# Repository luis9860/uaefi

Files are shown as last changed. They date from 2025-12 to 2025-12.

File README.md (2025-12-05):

# Ultra Affordable EFIi

🟢[$175 base model rusEFI store](https://www.shop.rusefi.com/shop/p/uaefi-ultra-affordable-efi)🟢

## Community Support

🔴Community support ONLY 🔴 https://www.facebook.com/groups/rusEfi 🔴 [Discord](https://github.com/rusefi/rusefi/wiki/Discord)🔴 [Commercial Support](https://www.shop.rusefi.com/shop/p/details-about-rusefi-ecu-technical-support) 🔴

## Technical Details

Open Source KiCAD hardware powered by [Hellen-One](https://github.com/andreika-git/hellen-one)

Powered by [rusEFI firmware](https://github.com/rusefi/rusefi)

[User Documentation](https://github.com/rusefi/rusefi/wiki/uaEFI)

x

x

## MCU options

1mb of flash is _required_.

One day we shall try https://jlcpcb.com/partdetail/Stmicroelectronics-STM32F427VIT6%2FC57097#EC or https://jlcpcb.com/partdetail/Stmicroelectronics-STM32F437VIT7%2FC1338578#EC

## rusEFI Store

https://www.shop.rusefi.com/shop/p/uaefi-ultra-affordable-efi

## HOWTO JLCPCB

You would need three files from ``boards/uaefi-a/board`` folder to place your JLCPB Assembly order: gerber.zip BOM-JLC.csv and CPL.csv

### Q: having trouble with opening uaefi board project. library path seems ok, i do not know how to solve missing modules issue

A: missing modules are closed source. they are filled in by github magic
github magic combines gerbers and spits out a complete bom/pcl/new gerbers to upload to jlc/friends. See https://github.com/rusefi/hellen-one/tree/master?tab=readme-ov-file#tldr for more info

### Q: Magic modules? How do I see schematics of those?

A: https://github.com/rusefi/hellen-one has full documentation for each module

### Q: Something wrong with BOM?

A: Nope, that's normal nothing to worry about click 'Continue'.



### Q: how do I get more RAM for Lua?

A: fabricate with STM32F42xVI firmware would defect extra RAM and give you extra Lua. Once your script does not fit into STM32F42xVI it's F7 time or help us leverage F413.

### Q: I've place an order with JLCPCB and I see scary looking wrong orientation?

A: that's expected. See [boards/uaefi-c/board](boards/uaefi-c/board) ``Original*.png`` files and ``Produce*.png`` after JLCPCB manual review process.

## Bluetooth power issue fix

It was found that board with installed BT module may be affected by power issue.

During power on BT module consume too much inrush current on 3.3V line causing 3.3V drop below MCU reset hreshold. This may lead to unstable start or infinity reset loop.

To fix this please install additional capacitors to 5V and 3.3V powerlines.

Polarized electrolytic capacitors with at least 10V rating and extended temperature range are recommended. Tantalum and solid electrolytic capacitors are also suitable.

**Please carefully follow illustrated polarity.**

33..47uF should be added to 5V powerrail. [This](https://www.digikey.com/en/products/detail/w%C3%BCrth-elektronik/860020372004/5727028) or [this](https://www.digikey.com/en/products/detail/w%C3%BCrth-elektronik/860080372001/5727224) or [any of these](https://www.digikey.com/en/products/filter/aluminum-electrolytic-capacitors/58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).



And 220..470uF should be added to 3.3V powerrail. [This](https://www.digikey.com/en/products/detail/w%C3%BCrth-elektronik/860010273011/5726952) or [this](https://www.digikey.com/en/products/detail/w%C3%BCrth-elektronik/860020273011/5727148) or [any of these](https://www.digikey.com/en/products/filter/aluminum-electrolytic-capacitors/58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).



## HOWTO EGT chip

This board has a placeholder for MAX31855 (or MAX6675) termocouple-to-digital chip. **This chip is not populated by default!**

Screenshot from 2025-09-26 11-15-15

D8 is **optional** ESD protection and also is not populated by default. You need to solder U4 only, D8 is optional. All passive components are already populated.

**MAX31855** works without addtional modification.

For **MAX6675** connect EGT- to GNDA either on J2 "C" connector or just short C28 (replace with 0R).

Screenshot from 2025-09-26 11-19-41

## [EXPERIMENTAL] How to make MAX9924 work with low tooth count trigger wheel

In some cases user may need two VR inputs on UAEFI and both trigger wheels are low-tooth count.

In default configuration MAX9924 does not work with low count trigger wheels because of its "adaptive peak threshold" and its watchdog.

Screenshot from 2025-10-12 16-58-30

On UAEFI MAX9924 is configured in **A2 mode**.

Screenshot from 2025-10-12 16-59-49

**B mode** allow use of MAX9924 with low count trigger wheels. But external Bias and Thresholt voltages should be allpied. Both can be sources from UAEFI Discrete VR module.

List of modifications:
1. pin 6: ZERO_EN connect to VCC instead of GND.
2. pin 4: supply 2.5 V instead of GND
3. pin 8: EXT, supply external threshold voltage

Pins 4 and 6 needs to be lifted from PCB to be disconnected from GND. Pin 8 initially is not connected to any circuit.

Use hot air gun to de-solder whole chip. Then twist pins 4 and 6 up so both do not touch PCB. Then solder chip back to PCB

Now use thin wire to connect:
1. pin 6 to pin 10 of the same chip.
2. pin 4 to **Vref** at R769 + C754. See file:///home/work/rusefi/docs/uaefi-d-ibom.html for its locations
3. pin 8 to **thresh_high** at U756 pin 1. See file:///home/work/rusefi/docs/uaefi-d-ibom.html for its locations



Now MAX9924 VR input uses same threshold vs RPM settings that is set for Descrete VR input. And it is cabable to work with low tooth count trigger wheels without noise issues.

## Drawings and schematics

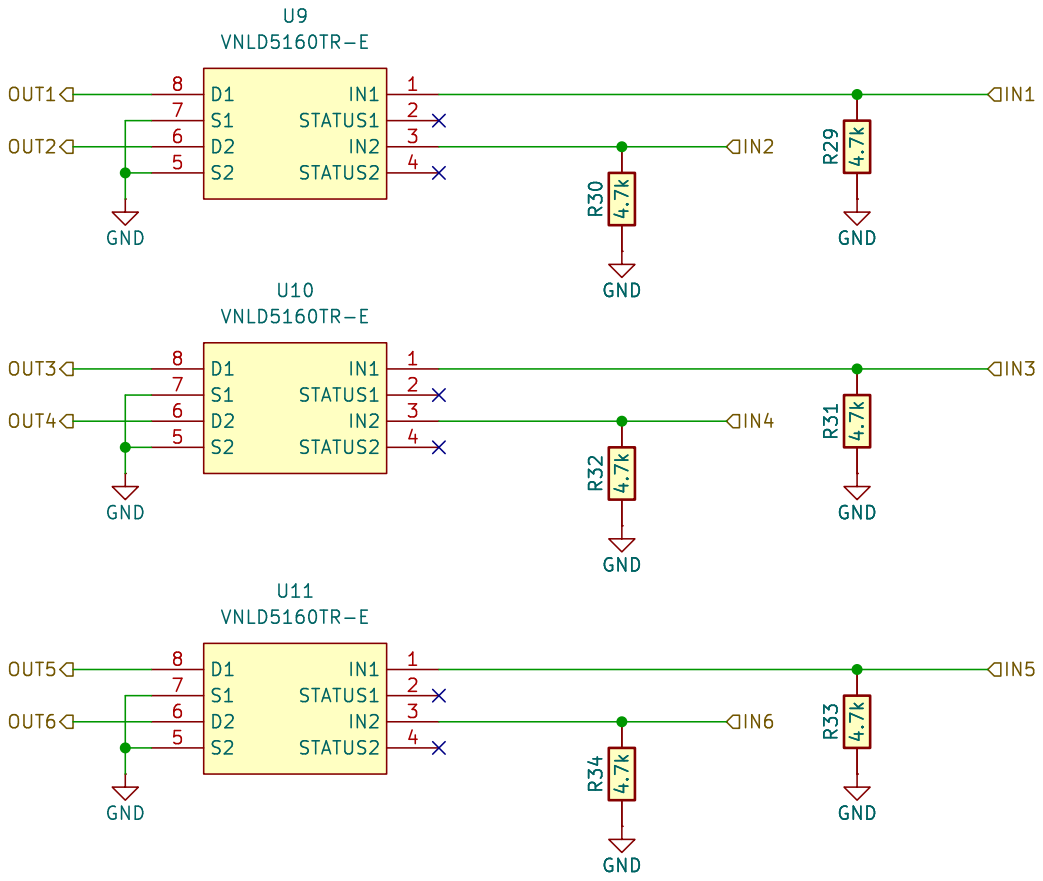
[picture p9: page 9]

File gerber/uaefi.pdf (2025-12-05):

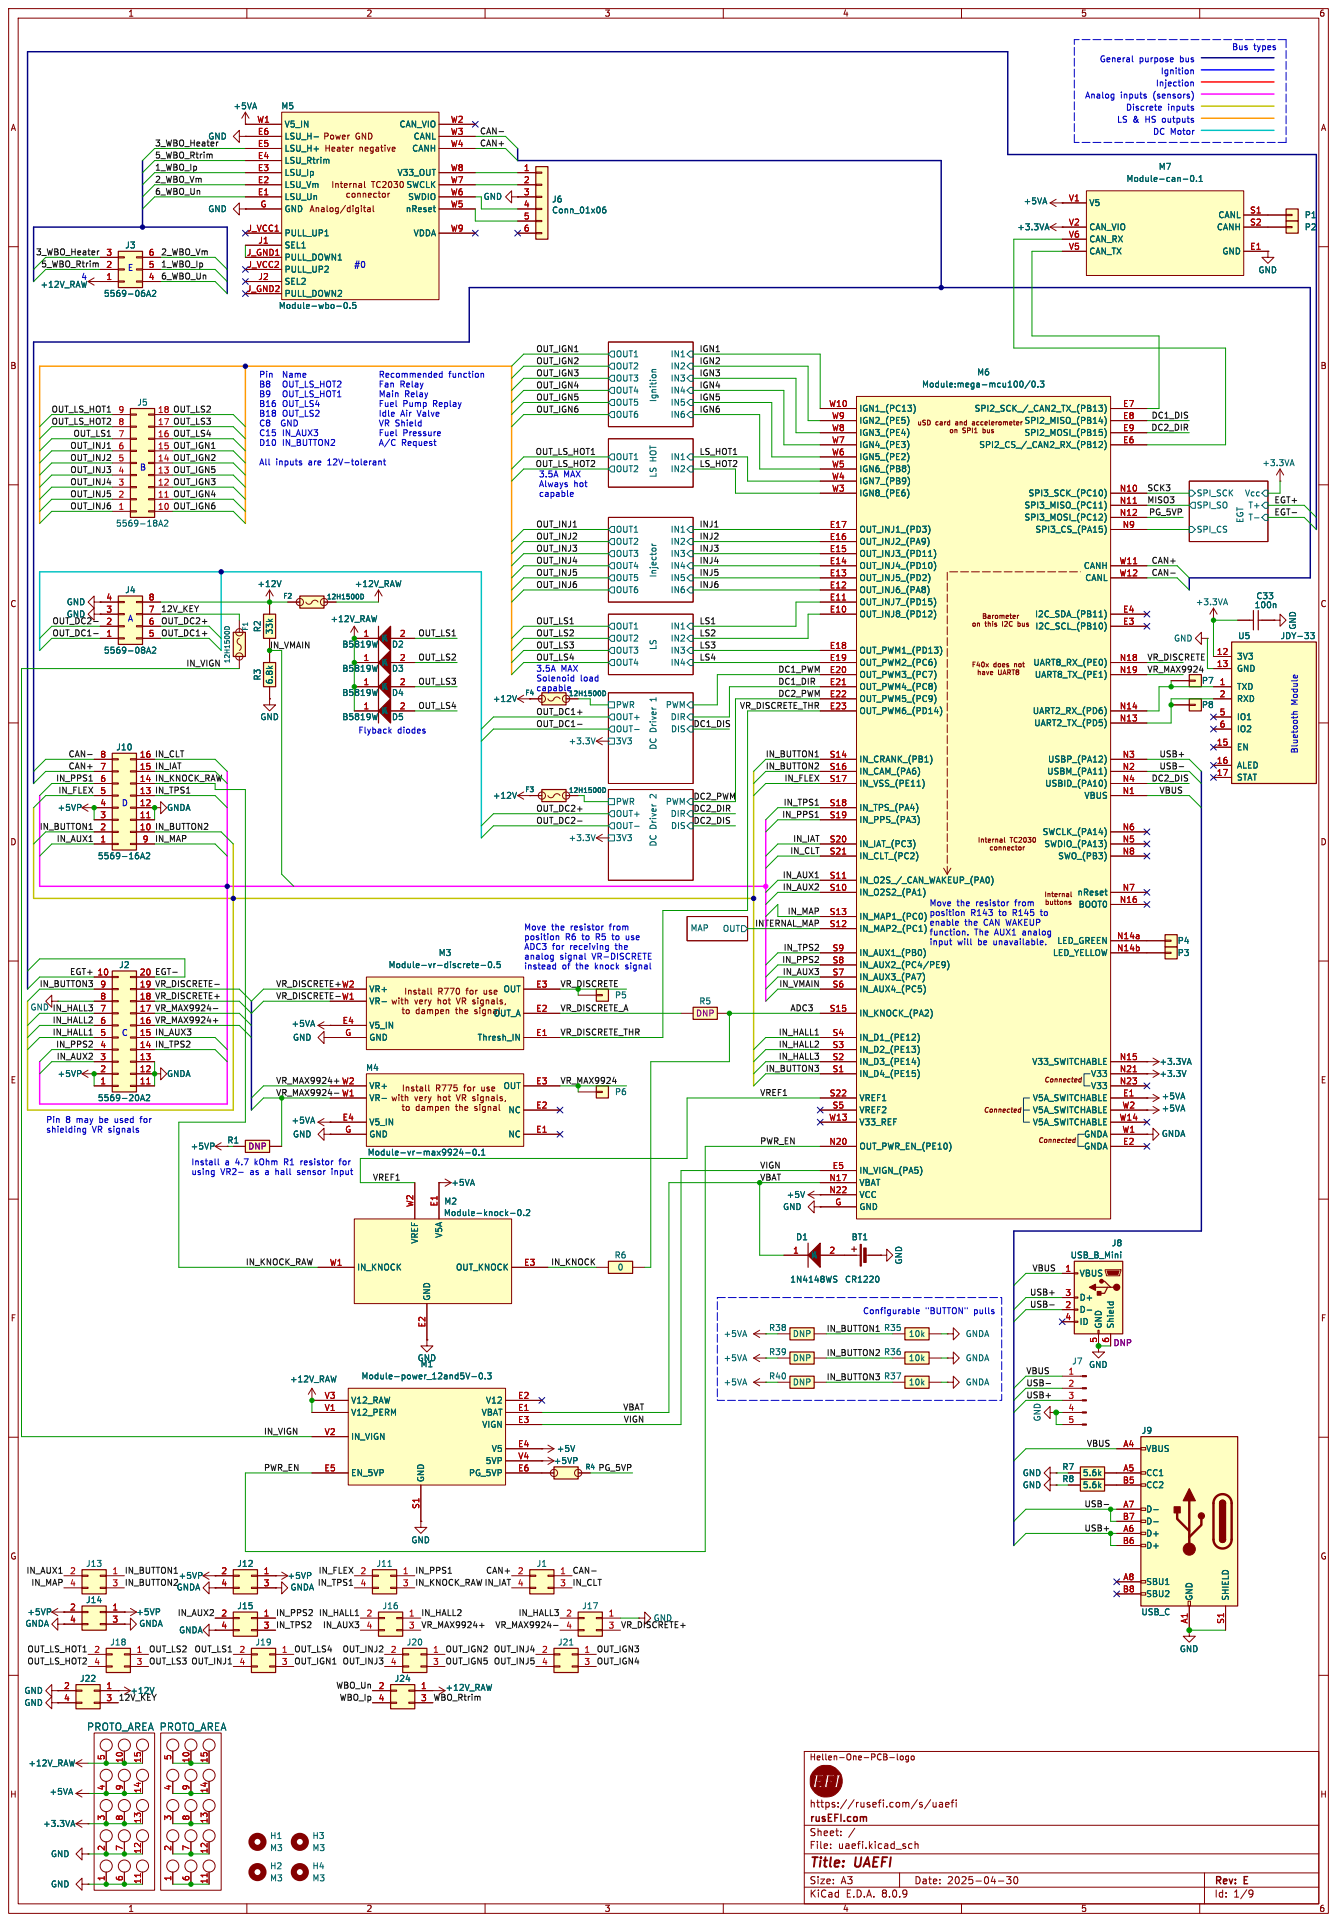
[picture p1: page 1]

Injection General purpose bus

Analog inputs (sensors) LS & HS outputs Discrete inputs A
8 +12V_RAW

Analog/digital Heater negative Power GND

3V3 12 GND 13 EN 15 ALED 16 STAT 17 RXD 2

enable the CAN WAKEUP

analog signal VR-DISCRETE

https://rusefi.com/s/uaefi
Id: 1/9 Title: UAEFI File: uaefi.kicad_sch Sheet: / rusEFI.com

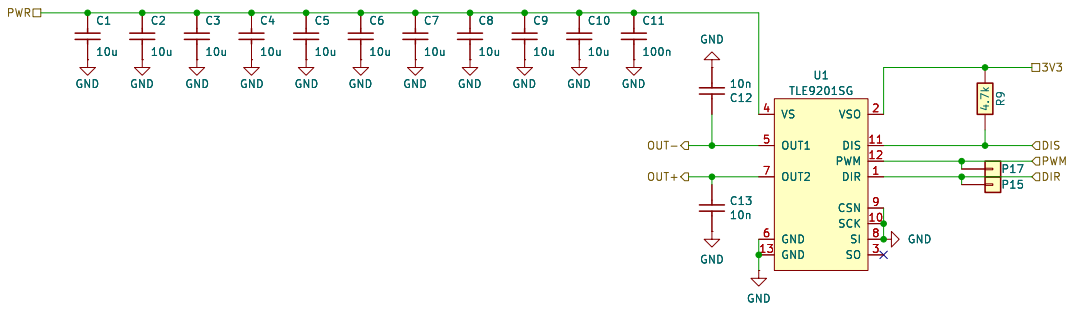
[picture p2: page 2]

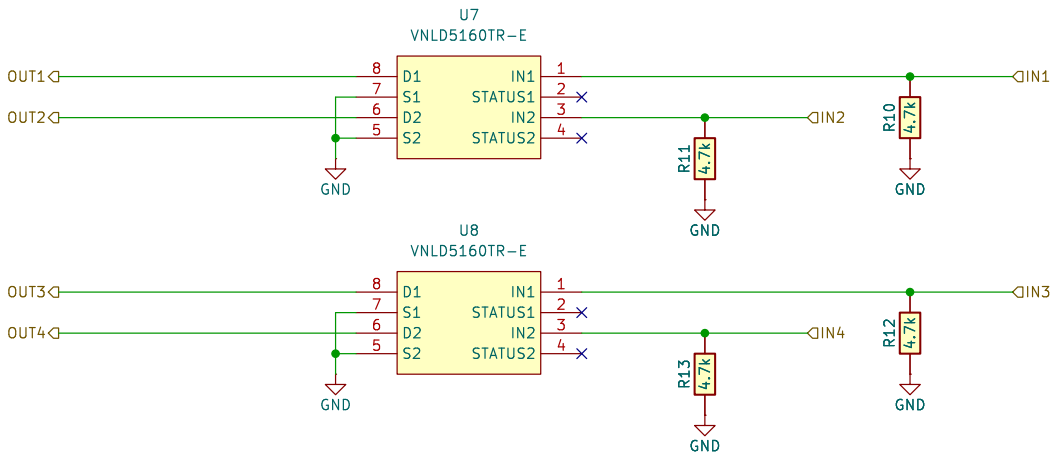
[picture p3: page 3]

Id: 3/9 Title: UAEFI File: LS4.kicad_sch Sheet: /LS/ rusEFI.com

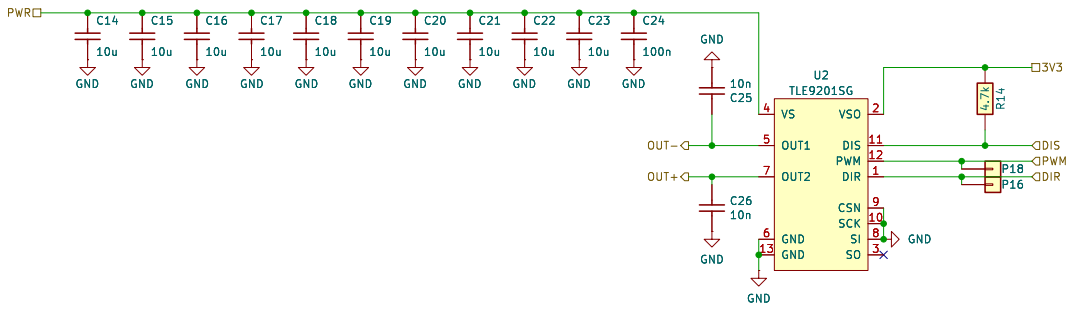
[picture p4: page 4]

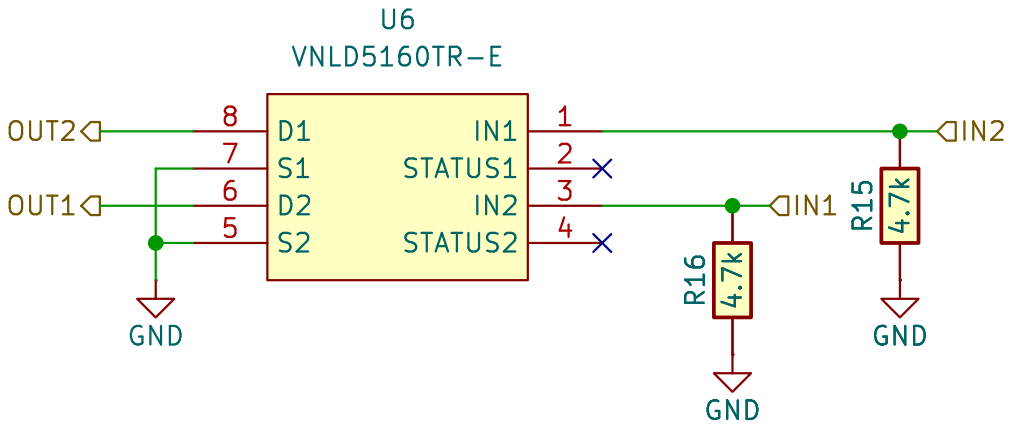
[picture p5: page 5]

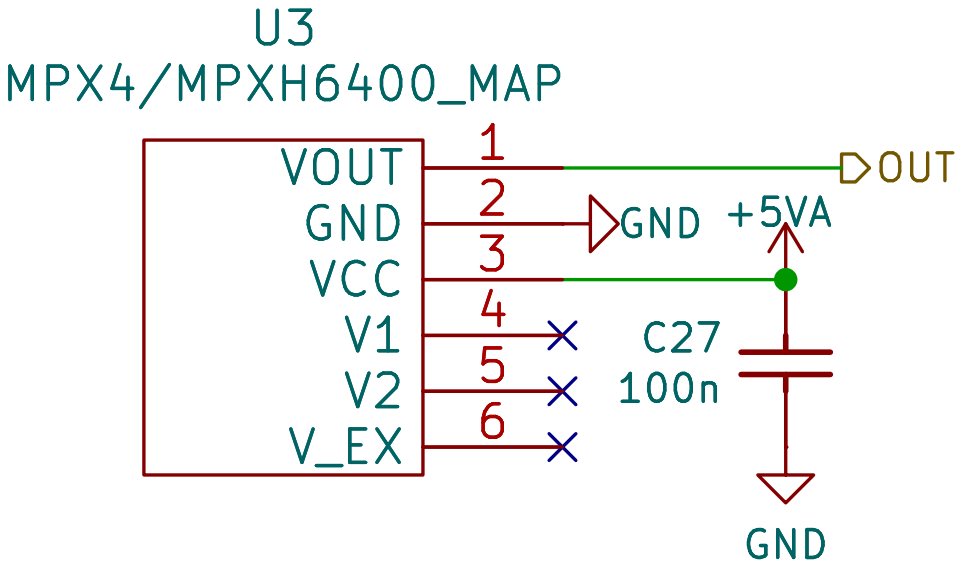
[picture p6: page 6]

Id: 8/9 Title: UAEFI File: MAP.kicad_sch Sheet: /MAP/ rusEFI.com

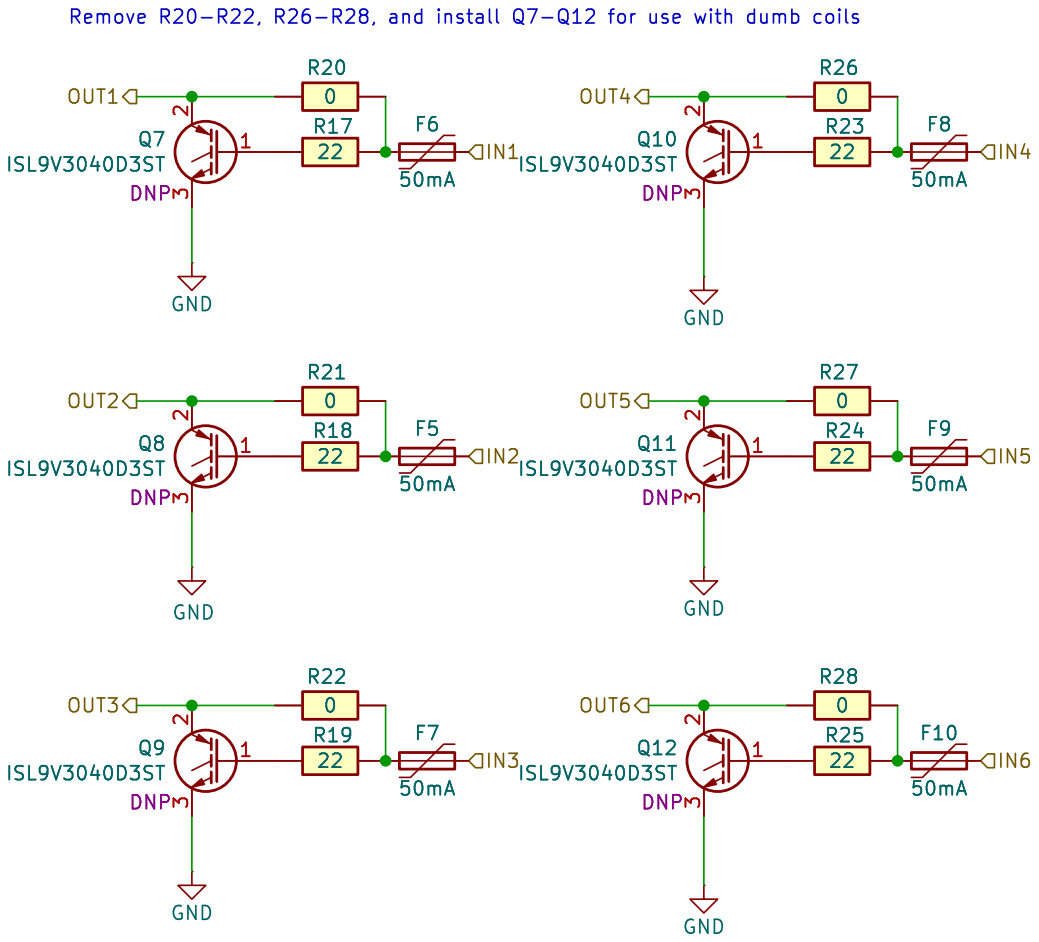
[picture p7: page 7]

Id: 9/9 Title: UAEFI File: IGN6.kicad_sch Sheet: /Ignition/ rusEFI.com

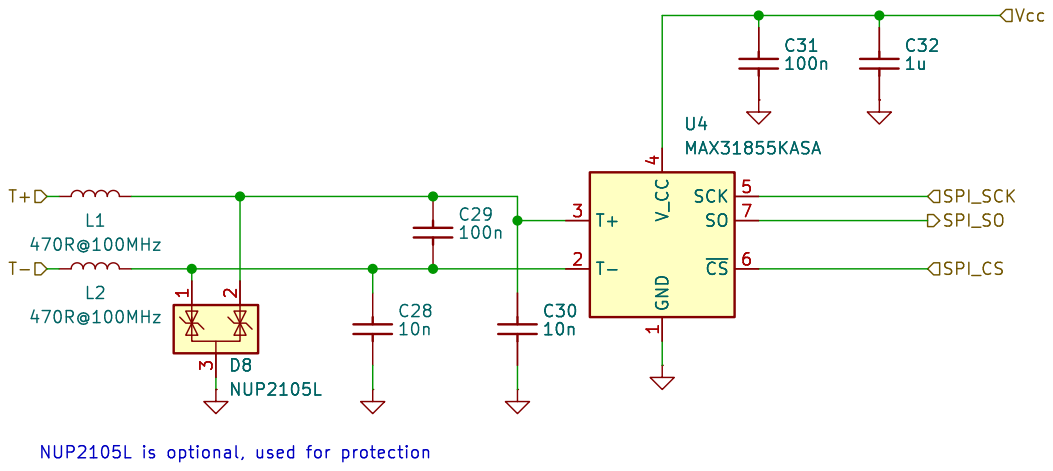
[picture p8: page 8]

Id: 9/9 Title: UAEFI File: egt.kicad_sch Sheet: /EGT/ rusEFI.com GND
